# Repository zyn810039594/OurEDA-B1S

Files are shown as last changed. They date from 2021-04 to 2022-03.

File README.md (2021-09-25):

# OurEDA-B1S

一个水下机器人（ROV/AUV）的下位仓控制系统

请使用Arduino、CubeMX、CubeIDE访问相关代码，使用AD打开硬件原理图和PCB Layout设计

### 目录说明

* Board 硬件电路图与PCB layout

  * CtrlBoard

    控制仓（主控仓）电路原理图与PCB layout

  * PowBoard

    电源仓大功率电源电路原理图与PCB layout

  * PowCtrlBoard

    电源仓（PWM控制仓）电路原理图与PCB layout

  * 部分处理姿态控制算法（使用PID）

  * 收集汇总传感器数据（间隔发送本仓传感器（比电源仓多加一个水深传感器）和电源仓传感器数据）

  * 将传感器数据传输到水面端或自主控制仓

  * 接收上位机指令

  * 将指令传给电源仓的H750进行执行

* Sensor

    * DeepF1

        水深传感器数据解析程序

        使用STM32F103C6T6

        * 专用于处理水深传感器的数据

        * 使用Arduino开发

    * GY-39

        温湿度传感器资料

    * P30

        声呐水深传感器资料

        * 使用submodule引用了一个上位机程序

    * WT931

        九轴传感器资料

* CtrlH7

  控制仓STM32H750程序

  * 部分处理姿态控制算法（使用PID）
  * 收集汇总传感器数据（间隔发送本仓传感器（比电源仓多加一个水深传感器）和电源仓传感器数据）
  * 将传感器数据传输到水面端或自主控制仓
  * 接收上位机指令
  * 将指令传给电源仓的H750进行执行

* PowH7

  电源仓控制板STM32H750程序

  * 进行温湿度气压、九轴传感器数据解析
  * 将传感器数据传输到控制仓的STM32H750
  * 接收上位机发送的PWM指令控制所有PWM输出

* MT7621

  机器人视频推流、串口网口转换、网络通讯中心设备

  使用成品MT7621路由器模块

  固件、软件配置、内核版本等

* Debug

  在调试过程中遇到重大Bug的解决方案

* Doc

  整体设计文档

* General

  上位机程序

* surface

  上位机内部Arduino程序

  * 使用Arduino获取操纵旋钮的信号

* DataFormat

  Debug时用到的一些上传/下传数据

### 文件说明

* UpFormat.xlsx

  上传数据格式

* DownFormat.xlsx

  下传指令格式

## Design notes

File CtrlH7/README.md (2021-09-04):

# 控制板STM32H750主程序

最新程序为`file_rebuild` ，移植了新版本的ROV驱动库

该仓的STM32负责漏水检测、温湿度大气压传感器、水深传感器、九轴的控制功能

同时可以自主实现PID定向定深

PID定向模式：保证ROV航向不变

PID定深模式：保证ROV所处深度不变

使用FreeRTOS进行任务调度，但仅仅使用了其中的任务调度功能，并未使用信号量、消息队列等功能（主要是因为原作者懒得用），下一迭代可能会考虑充分使用这些功能以增强系统稳定性

主要文件：

* main.c：分配任务和基本控制逻辑
* BasicCtrl.c：基本控制函数库文件，一直沿用到现在的推进器控制代码
* Sensor.c：传感器处理函数库文件

## 初步测试结果

1. 上电后stm32h7无任何反应
2. 温湿度传感器输出正常
3. 九轴传感器输出正常
4. 深度解算板（stm32f1）输出正常
5. MT7621工作正常，但WAN口无法连接外网，所有LAN口正常工作
6. USB无法连接
7. openwrt开机缓慢

准备进行初步Debug

### Dubug结果

1. 修复路由器模块WAN口问题、USB问题
2. 重新刷写openwrt固件到19.07版本
3. 成功安装需要的软件
4. 修复stm32h750所有问题

## 再次测试结果

1. stm32h750上传数据、下传指令功能正常
2. 未验证上传数据内容是否正常，但是指令长度、传感器变化、开始标志位、结束标志位均存在，待后续测试
3. 未验证下传指令速率，存在未上电时控制指令紊乱的情况
4. 通常USB设备可以连接，但无法连接uvc免驱USB摄像头
5. openwrt可以接收到串口数据，但未测试串口转网口功能
6. openwrt其他功能正常

### 上传数据测试结果

1. 湿度上传**可能**存在问题（正常值60，传感器上报80）
2. 水深上传存在问题
3. 欧拉角上传可能存在问题

### Bug修复结果

1. 修复温湿度大气压传感器数据问题
2. 可能修复欧拉角上传数据问题
3. **发现水深水温传感器数据传输卡死**

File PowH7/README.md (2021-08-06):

# PWM-传感器控制板程序

位于推进器控制仓的STM32主要负责控制PWM输出和接收一部分传感器数据

最新程序为`file_rebuild`，修复了很多问题，并合理使用了FreeRTOS的互斥量、信号量，避免使用全局变量

## 初步测试结果

1. PWM输出正常
2. 传送带PWM输出正常
3. 由于PCB设计问题，继电器无法控制
4. 机械臂PWM缺少两路输出（其他四路工作正常），怀疑缺少上位机指令导致
5. 缺少灯光PWM输出，初步怀疑缺少上位机指令导致
6. 缺少云台PWM输出，初步怀疑缺少上位机指令导致
7. 缺少上传串口信息（两次检测中一次可以读取到十六进制数据，一次无法读取），经检测传感器并未损坏，怀疑是程序问题

## 最终测试结果

1. 修复了继电器问题
2. 数字隔离器损坏导致灯光、云台缺少输出，已修复
3. 机械臂PWM缺少两路输出，修复其中一路（为软件问题），另一路暂时未能修复，原因不明
4. 缺少上传串口信息，怀疑是程序问题
5. 暂未发现其他问题

### Debug结果

1. 通过外挂自制的光耦-继电器模块彻底修复继电器问题
2. 修复所有PWM
3. 发现串口程序问题，无法正常从传感器读取数据上传，准备修复

## 实机测试结果

1. 修复了串口程序问题
2. 基本控制功能正常
3. 无法控制灯光PWM
4. 未验证串口信息发送准确性

### Dubug结果

1. 灯光只能使用4.2V以上电压驱动（典型值5V）
2. 发生串口控制失灵时不灵的情况，怀疑是调整为50Hz的PWM信号问题，已经改回

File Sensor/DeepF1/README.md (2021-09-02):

# 深度数据解析

使用Arduino对STM32F103进行开发

### 依赖库

1. Arduino IDE
2. [Arduino_STM32扩展](https://github.com/rogerclarkmelbourne/Arduino_STM32)
3. MS5883 Arduino库

## 初步测试结果

能够按照既定格式向STM32H750发送解析后的深度数据

## 测试结果

***测试通过***

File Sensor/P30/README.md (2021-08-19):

# 声呐

连接到控制板的stm32上

使用串口UART5

这里引用了一个官方的上位机源码ping-viewer

使用

```shell
git submodule init
git submodule pull
```

拉取submodule

[参考资料](https://searobotix.com/p30-sonar/)

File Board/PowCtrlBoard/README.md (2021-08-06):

# PWM-传感器控制板硬件设计

使用一个STM32H750接收上位机发送的控制数据并控制推进器、云台等PWM输出

同时该MCU会收取传感器上传的数据，解析后再传输给控制板的STM32或AUV控制单元或上位机

## 初步测试结果

继电器控制电路出错

### Debug结果

已对继电器控制电路进行修改，加入洞洞板焊接的光耦-继电器控制电路，参照如下电路设计，但将继电器放在接地一端，采用共地驱动

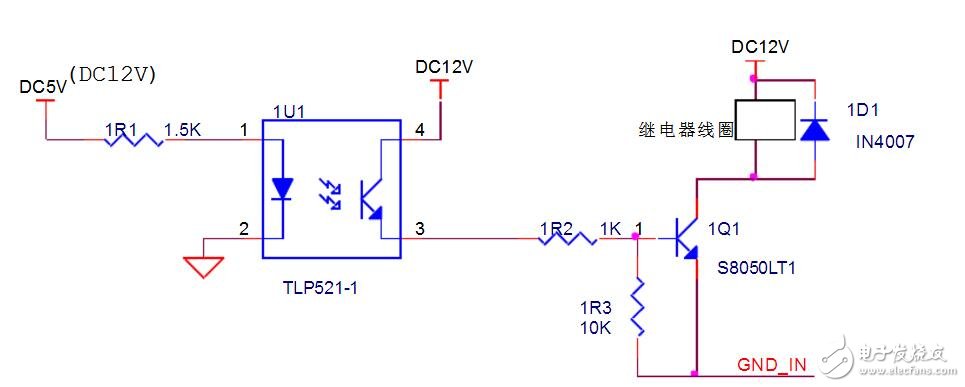
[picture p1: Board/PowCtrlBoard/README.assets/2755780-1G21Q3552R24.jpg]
光耦驱动继电器电路图大全（光电耦合器/ULN2803 /开关电路）


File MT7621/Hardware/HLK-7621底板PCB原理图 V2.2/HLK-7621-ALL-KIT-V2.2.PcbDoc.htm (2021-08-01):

Reporting Options

# File in Previous Format

Date | : | 2021/6/21
Time | : | 10:18:27
Filename | : | E:\HLK\模块资料\资料\wifi模块\HLK-7621A\HLK-7621底板PCB原理图 V2.2\HLK-7621-ALL-KIT-V2.2.PcbDoc

Version | Warning
Summer 09 | CAUTION - File contains old violation objects. These violations are no longer supported & will not be loaded. Please run DRC after opening this file in order to refresh the violations.
Summer 09 | CAUTION - Existing testpoint rules and settings are used as fabrication testpoint information.
Release 12 | CAUTION - Air Gap Width previously controlled by Clearance rule is now controlled by Polygon Connect Style rule's newly introduced Air Gap Width (set to default value). Suggest reviewing each Polygon Connect Style rule's Air Gap Width attribute for correctness.
Release 13 | CAUTION - Silkscreen Over Component Pads Rules are converted to Silk To Solder Mask Clearance Rules. Suggest examining rule scopes for accuracy.

This file was generated by an earlier version of the software

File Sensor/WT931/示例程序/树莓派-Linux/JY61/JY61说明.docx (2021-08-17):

1.给树莓派 连接电源和网线

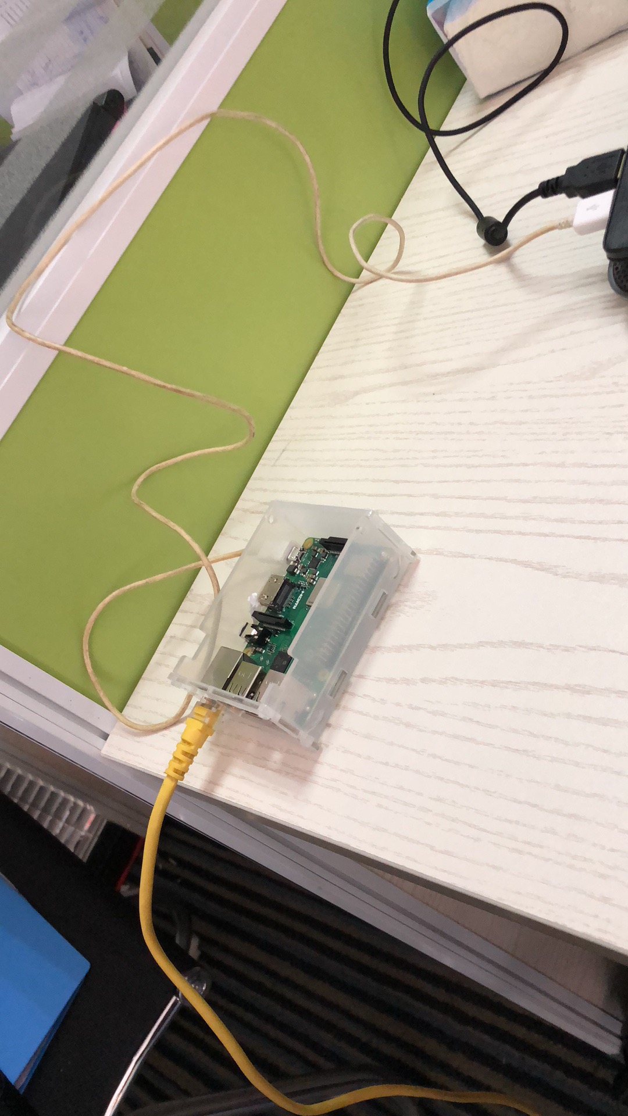
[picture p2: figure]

2.连接上树莓派和JY61的模块（注意六合一串口模块拨码1为ON、拨码2为OFF，开关S1置other ；JY61模块跟六合一串口模块引脚需要一一对应，VCC对3V3,RX对TX，TX对RX，GND对GND）

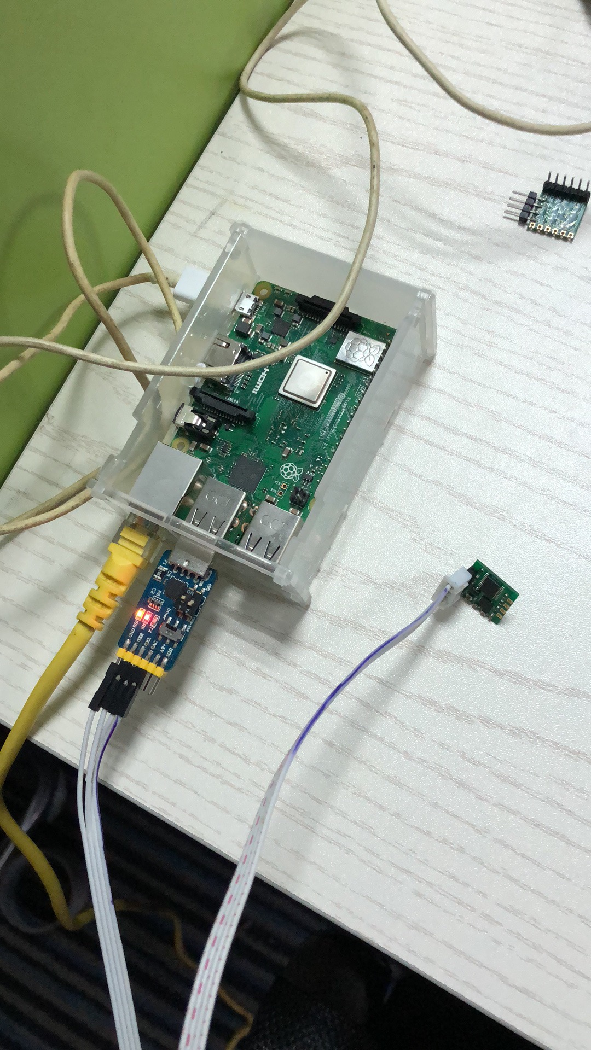
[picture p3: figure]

3.前往官网下载VNC，官网地址：https://www.realvnc.com/en/

软件安装步骤参考官网安装步骤，在下载的文件夹VNC Viewer中打开vncviewer.exe

在这里输入树莓派的ip地址（可通过ip搜索器搜索，选择ip名为raspberrypi的ip地址）

（## IP搜索器可自行百度下载）

4.输入账号密码， 账号：**** 密码：****

账号密码参考自己的树莓派资料

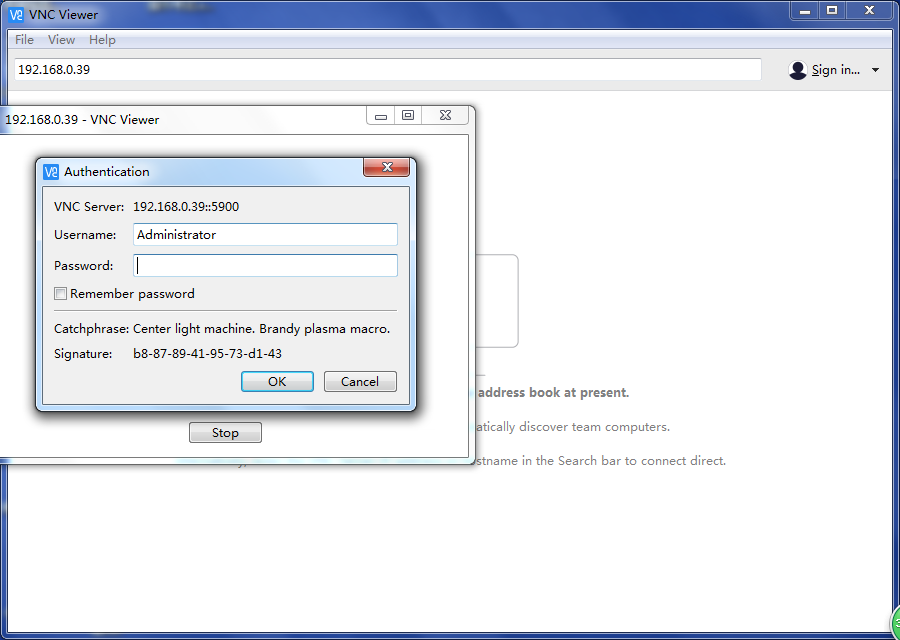
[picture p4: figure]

5.在上中方上传电脑的示例代码文件到树莓派中

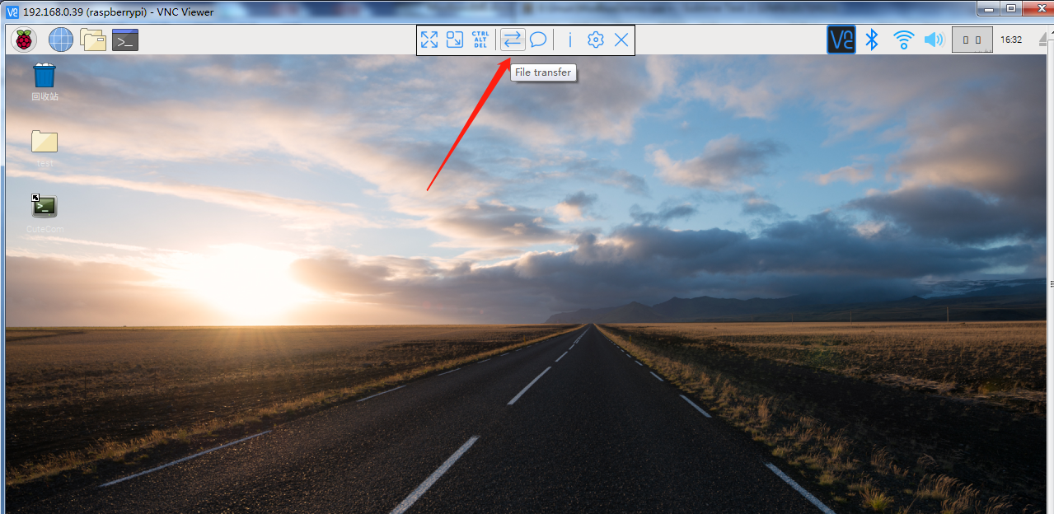
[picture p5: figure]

6.拷贝完成后，打开终端对桌面进行

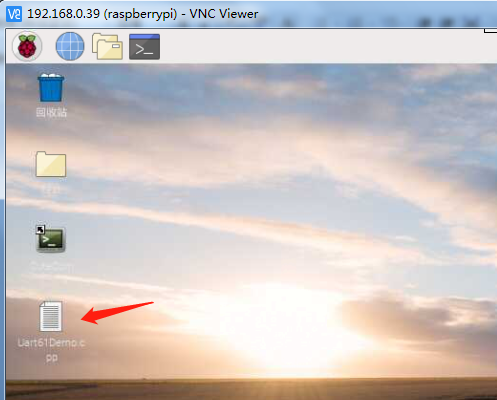
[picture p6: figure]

7.注：右键可打开终端

终端中的Desktop文件夹即为桌面

编辑：gcc Uart61Demo.cpp -o Uart61Demo

运行：./ Uart61Demo

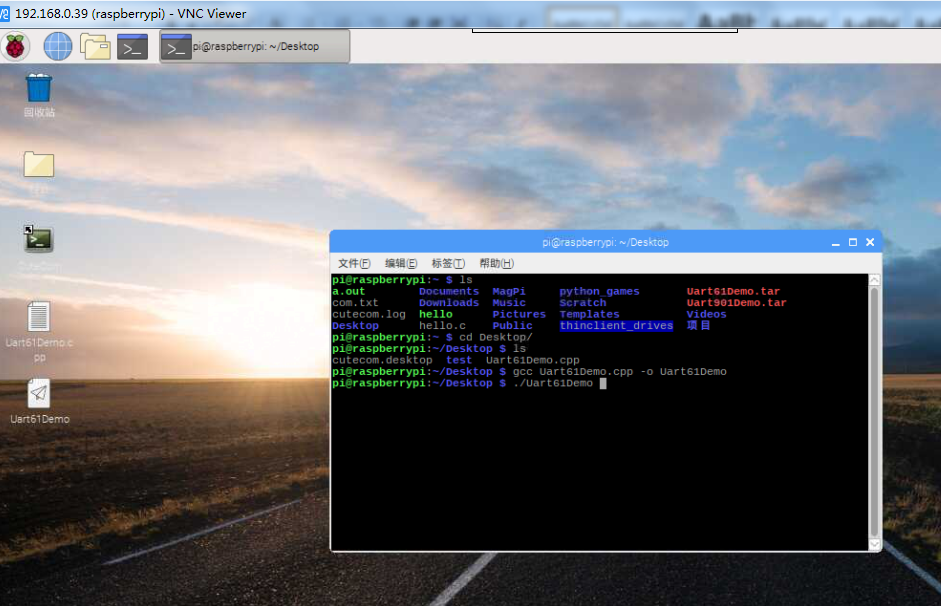
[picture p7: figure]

8.结果展示

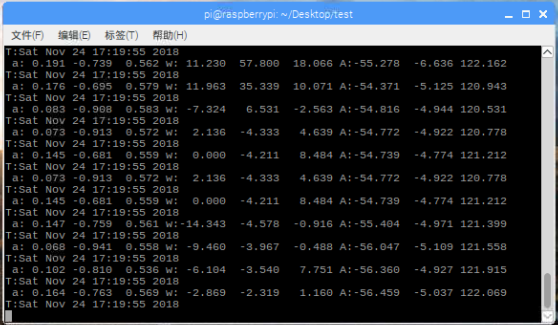
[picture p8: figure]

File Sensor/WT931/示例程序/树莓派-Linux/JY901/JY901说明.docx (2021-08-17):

1.给树莓派 连接电源和网线


2.连接上树莓派和JY901的模块（注意六合一串口模块拨码1为ON、拨码2为OFF，开关S1置other ；JY901模块跟六合一串口模块引脚需要一一对应，VCC对3V3,RX对TX，TX对RX，GND对GND）

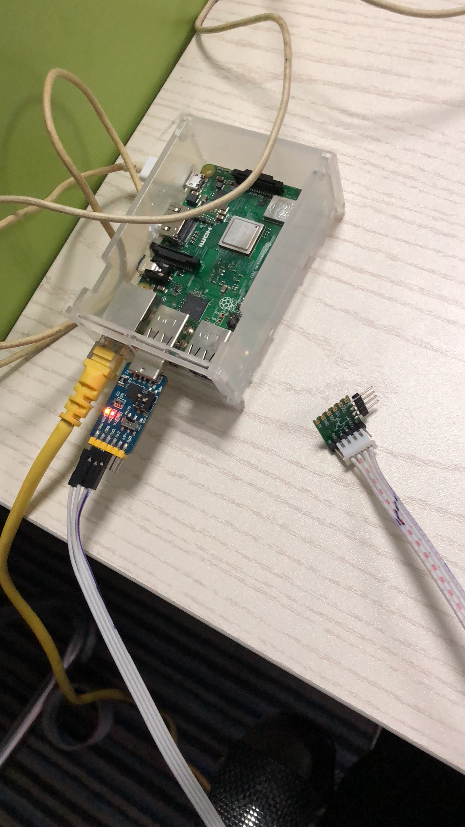
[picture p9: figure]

3.前往官网下载VNC，官网地址：https://www.realvnc.com/en/

软件安装步骤参考官网安装步骤，在下载的文件夹VNC Viewer中打开vncviewer.exe

在这里输入树莓派的ip地址（可通过ip搜索器搜索，选择ip名为raspberrypi的ip地址）

（## IP搜索器可自行百度下载）

4.输入账号密码， 账号：**** 密码：****

账号密码参考自己的树莓派资料


5.在上中方上传电脑的示例代码文件到树莓派中


6.拷贝完成后，打开终端对桌面进行

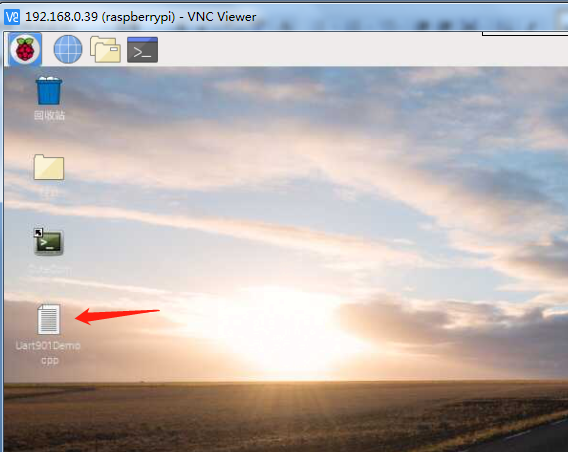
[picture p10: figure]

7.注：右键可打开终端

终端中的Desktop文件夹即为桌面

编辑：gcc Uart901Demo.cpp -o Uart901Demo

运行：./ Uart901Demo

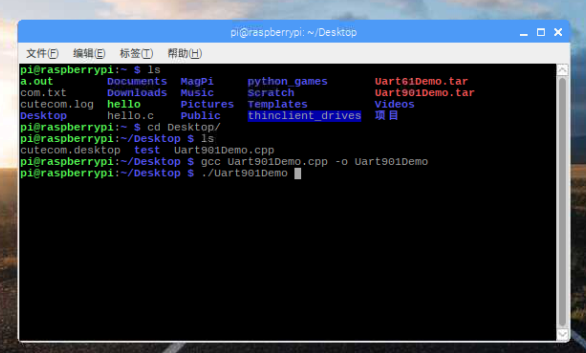
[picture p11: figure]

8.结果展示

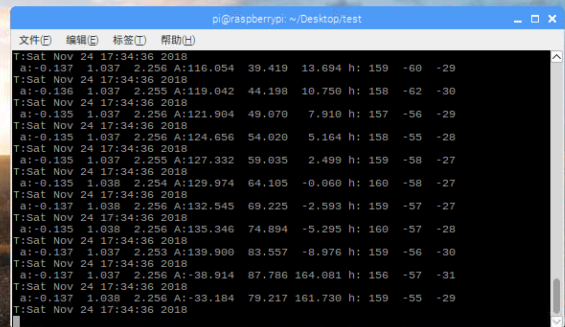
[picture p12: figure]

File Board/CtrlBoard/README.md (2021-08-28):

# 控制板与电源板硬件设计

**horziontal**：第一版叠层5V/3.3V电源板，已废弃

Fatal：存在功率电感容易过流损坏的问题

**horziontal_v2**：第二版叠层5V/3.3V电源板，采用大功率绕线电感并优化了布线

Debug：修正了电感画错（没有旋转90度导致大短路）的问题

**vertical**：直插5V/3.3V电源板，测试阶段未见Bug

Fatal：老师觉得难看

**Processor**：包含PRO和PRO2两版主控板设计，PRO单纯作为留档，PRO2修正了PRO中存在的一些问题。

Debug：IIC接口添加4.7K上拉电阻

Debug：添加JTAG接口

Debug：添加可选的AMS1117辅助供电

**ProConnect**：网口、摄像头转接板

Debug：JP3所接WAN口无法使用（有供电但无信号传输），暂时无法确认是否为PCB问题

Debug：WAN口Bob-Smith电路没有焊好导致无信号，已经修复

### 几个板子都是新手/随意走线，高血压警告

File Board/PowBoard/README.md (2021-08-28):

# 总电源板硬件设计

使用多个堆叠的大功率稳压输出模块输出12V-60A（max），以供给推进器、舵机，并通过`【CtrlBoard】-【horziontal】和【vertical】`两个稳压隔离电源模块输出5V和3.3V为MCU和传感器供电

电路走线使用8oz特殊规格加镀锡铜排加强功率性能

尚未进行测试⚠

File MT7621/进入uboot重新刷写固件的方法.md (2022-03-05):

1. 连接LAN口到上位机
2. 修改LAN口的上位机ip为静态`10.10.10.3`，子网掩码为`255.255.0.0`
3. 将openwrt断电
4. 按住sw_wps按键
5. openwrt上电
6. 保持按键1min
7. 松开按键
8. 打开`10.10.10.123`
9. 选择固件并进行上传
10. 等待2min以上
11. 修改LAN口ip为dhcp模式
12. 尝试连接`192.168.1.1`或`192.168.16.254`或`192.168.1.254`

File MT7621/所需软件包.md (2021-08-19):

1. 推流
   * usb摄像头驱动

     * kmod-usb2
     * kmod-usb-uhci
     * kmod-usb-ohci
     * libv4l
     * kmod-video-core
     * kmod-video-videobuf2
     * kmod-video-uvc
     * kmod-video-pwc
     * kmod-video-gspca-core
     * kmod-video-cpia2
     * kmod-video-gspca-*（有关的包全部安装）

   * mjpg-streamer推流与luci控制

     * mjpg-streamer
     * luci-app-mjpg-streamer
     * luci-i18n-mjpg-streamer-zh-cn

2. 串口-tcp报文转换
   
   * ser2net
   
3. debug工具
   
   * usbutils
   * vim/vi
   * minicom

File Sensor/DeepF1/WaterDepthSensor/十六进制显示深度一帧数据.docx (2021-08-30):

54 3D 32 32 2E 32 35 44 3D 2D 30 2E 30 30 0D 0A

54 3D 32 32 2E 32 39 44 3D 30 2E 30 30 0D 0A

54 3D 32 32 2E 33 32 44 3D 30 2E 30 30 0D 0A

0 1 2 3 4 5 6 7 8 9 10 11 12 13 14

54 3D 32 30 2E 35 33 44 3D 2D 30 2E 30 31 0D 0A3D2E

T = int16 . int16 D = int16 . int16 \r \n

int16[10];

u8 data[16];

大致分析如下

54→‘T’

3D→‘=’

2E→‘.’

44→‘D’

3D→‘=’

2D→‘-’

OD→‘\r’

OA→’\n’

收到的都是字符串，需要转换成十六进制

T | = | int16 | | . | int16 | | D | = | | | . | int16 | | \r | \n
54 | 3d | | | 2e | | | 44 | 3d | | | 2e | | | 0d | 0a
0 | 1 | 2 | 3 | 4 | 5 | 6 | 7 | 8 | 9 | 10 | 11 | 12 | 13 | 14 | 15

T | = | int16 | | . | int16 | | D | = | - | . | int16
54 | 3d | 32 | 32 | 2e | 35 | 35 | 44 | 3d | 2d | 2e | 30 | 30 | 35 | d
0 | 1 | 2 | 3 | 4 | 5 | 6 | 7 | 8 | 9 | 10 | 11 | 12 | 13 | 14

54 3d 32 32 2e 35 35 44 3d 2d 2e 30 30 35 d

0 1 2 3 4 5 6 7 8 9 10 11 12 13 15

T=22.70D=0.03

T=22.70D=0.04

T=22.71D=0.03

T=22.70D=0.03

T=22.70D=0.03

T=22.71D=0.03

T=22.70D=0.03

T=22.71D=0.03

T=22.71D=0.04

T=22.71D=0.03

T=22.71D=0.03

T=22.71D=0.03

T=22.71D=0.03

T=22.71D=0.03

T=22.71D=0.03

T=22.71D=0.04

T=22.71D=0.03

T=22.71D=0.03

T=22.71D=0.04

T=22.71D=0.03

T=22.71D=0.03

54 3D 32 32 2E 37 30 44 3D 30 2E 30 33 0D 0A

54 3D 32 32 2E 36 39 44 3D 30 2E 30 33 0D 0A

54 3D 32 32 2E 37 30 44 3D 30 2E 30 33 0D 0A

54 3D 32 32 2E 37 30 44 3D 30 2E 30 33 0D 0A

54 3D 32 32 2E 37 30 44 3D 30 2E 30 33 0D 0A

54 3D 32 32 2E 37 30 44 3D 30 2E 30 33 0D 0A

54 3D 32 32 2E 36 39 44 3D 30 2E 30 34 0D 0A

54 3D 32 32 2E 37 30 44 3D 30 2E 30 34 0D 0A

54 3D 32 32 2E 37 30 44 3D 30 2E 30 34 0D 0A

54 3D 32 32 2E 37 30 44 3D 30 2E 30 34 0D 0A

54 3D 32 32 2E 37 30 44 3D 30 2E 30 33 0D 0A

54 3D 32 32 2E 37 30 44 3D 30 2E 30 33 0D 0A

54 3D 32 32 2E 37 30 44 3D 30 2E 30 33 0D 0A

54 3D 32 32 2E 37 30 44 3D 30 2E 30 34 0D 0A

54 3D 32 32 2E 37 30 44 3D 30 2E 30 34 0D 0A

54 3D 32 32 2E 37 30 44 3D 30 2E 30 34 0D 0A

54 3D 32 32 2E 37 30 44 3D 30 2E 30 33 0D 0A

54 3D 32 32 2E 37 30 44 3D 30 2E 30 33 0D 0A

54 3D 32 32 2E 37 30 44 3D 30 2E 30 33 0D 0A

54 3D 32 32 2E 37 30 44 3D 30 2E 30 33 0D 0A

54 3D 32 32 2E 37 30 44 3D 30 2E 30 33 0D 0A

54 3D 32 32 2E 37 30 44 3D 30 2E 30 34 0D 0A

54 3D 32 32 2E 37 30 44 3D 30 2E 30 33 0D 0A

54 3D 32 32 2E 37 30 44 3D 30 2E 30 34 0D 0A

54 3D 32 32 2E 37 31 44 3D 30 2E 30 33 0D 0A

54 3D 32 32 2E 37 30 44 3D 30 2E 30 33 0D 0A

54 3D 32 32 2E 37 30 44 3D 30 2E 30 33 0D 0A

54 3D 32 32 2E 37 31 44 3D 30 2E 30 33 0D 0A

54 3D 32 32 2E 37 30 44 3D 30 2E 30 33 0D 0A

54 3D 32 32 2E 37 31 44 3D 30 2E 30 33 0D 0A

54 3D 32 32 2E 37 31 44 3D 30 2E 30 34 0D 0A

54 3D 32 32 2E 37 31 44 3D 30 2E 30 33 0D 0A

54 3D 32 32 2E 37 31 44 3D 30 2E 30 33 0D 0A

54 3D 32 32 2E 37 31 44 3D 30 2E 30 33 0D 0A

54 3D 32 32 2E 37 31 44 3D 30 2E 30 33 0D 0A

54 3D 32 32 2E 37 31 44 3D 30 2E 30 33 0D 0A

54 3D 32 32 2E 37 31 44 3D 30 2E 30 33 0D 0A

54 3D 32 32 2E 37 31 44 3D 30 2E 30 34 0D 0A

54 3D 32 32 2E 37 31 44 3D 30 2E 30 33 0D 0A

54 3D 32 32 2E 37 31 44 3D 30 2E 30 33 0D 0A

54 3D 32 32 2E 37 31 44 3D 30 2E 30 34 0D 0A

54 3D 32 32 2E 37 31 44 3D 30 2E 30 33 0D 0A

54 3D 32 32 2E 37 31 44 3D 30 2E 30 33 0D 0A

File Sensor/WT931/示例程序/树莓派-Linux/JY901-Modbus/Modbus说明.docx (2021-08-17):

1.给树莓派 连接电源和网线


2.连接上树莓派和485系列的模块（注意六合一串口模块拨码1、拨码2都为ON，开关S1置other ；485系列模块跟六合一串口模块引脚需要一一对应，VCC对3V3,A对A，B对B，GND对GND）

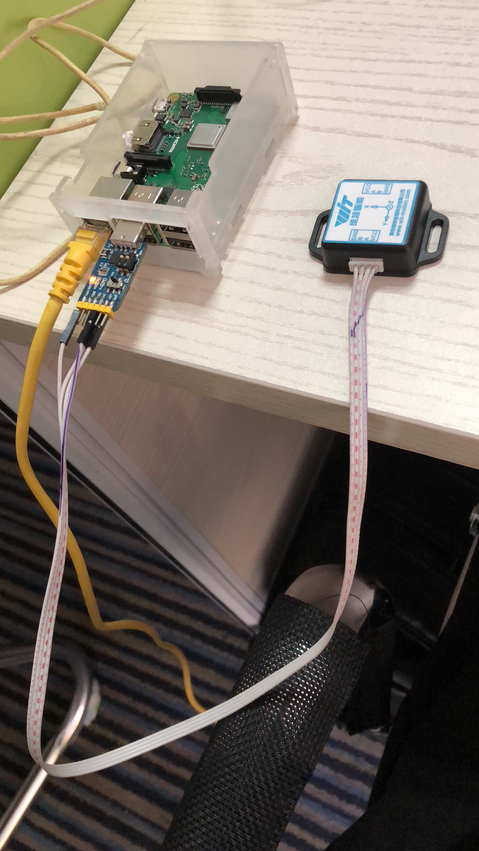
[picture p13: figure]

3.前往官网下载VNC，官网地址：https://www.realvnc.com/en/

软件安装步骤参考官网安装步骤，在下载的文件夹VNC Viewer中打开vncviewer.exe

在这里输入树莓派的ip地址（可通过ip搜索器搜索，选择ip名为raspberrypi的ip地址）

（## IP搜索器可自行百度下载）

4.输入账号密码， 账号：**** 密码：****

账号密码参考自己的树莓派资料


5.在上中方上传电脑的示例代码文件到树莓派中


6.拷贝完成后，打开终端对桌面进行

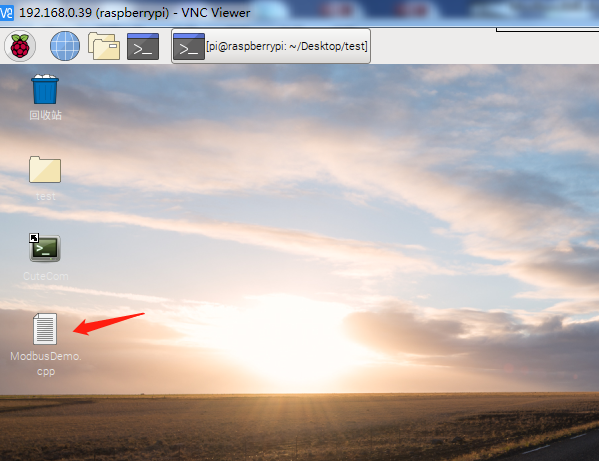
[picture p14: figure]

7.注：右键可打开终端

终端中的Desktop文件夹即为桌面

编辑：gcc ModbusDemo.cpp -o ModbusDemo

运行：./ModbusDemo

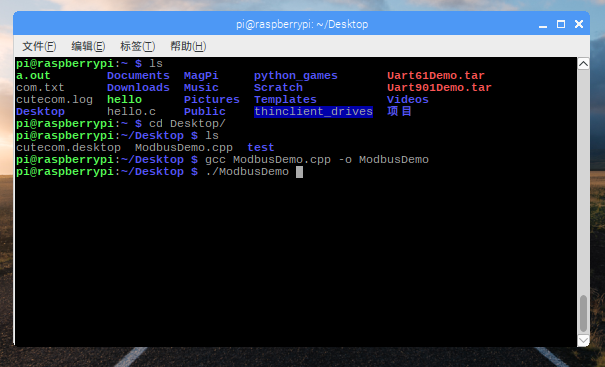
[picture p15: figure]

8.结果展示

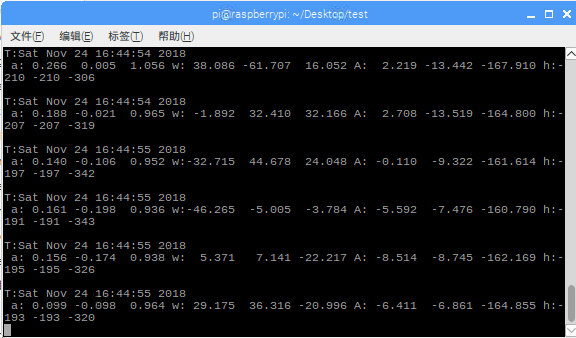
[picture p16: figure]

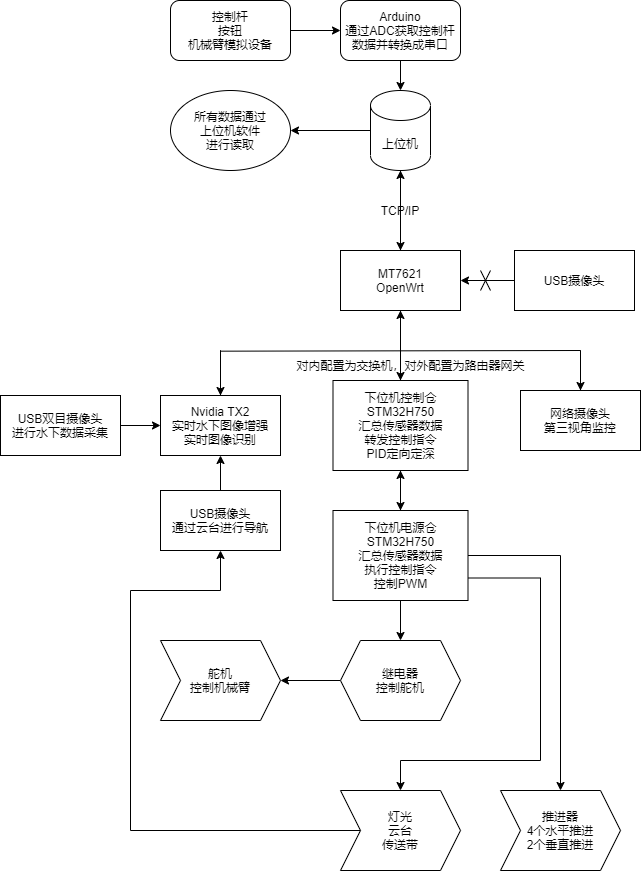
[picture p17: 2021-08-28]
Doc/General.png

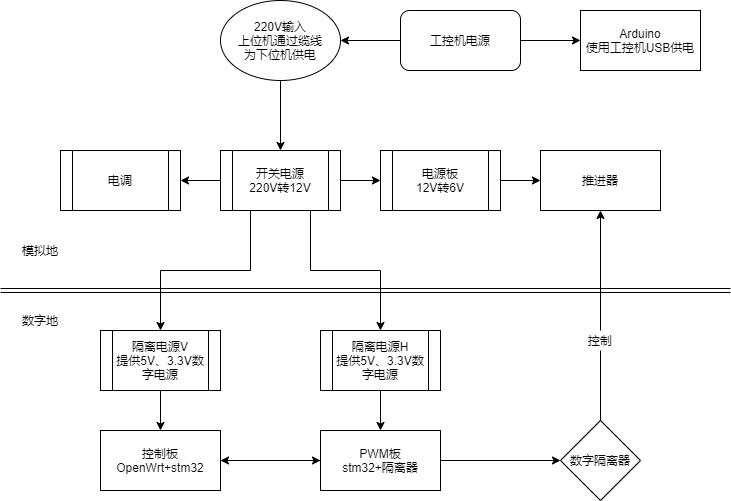
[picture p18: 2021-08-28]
Doc/Power.png

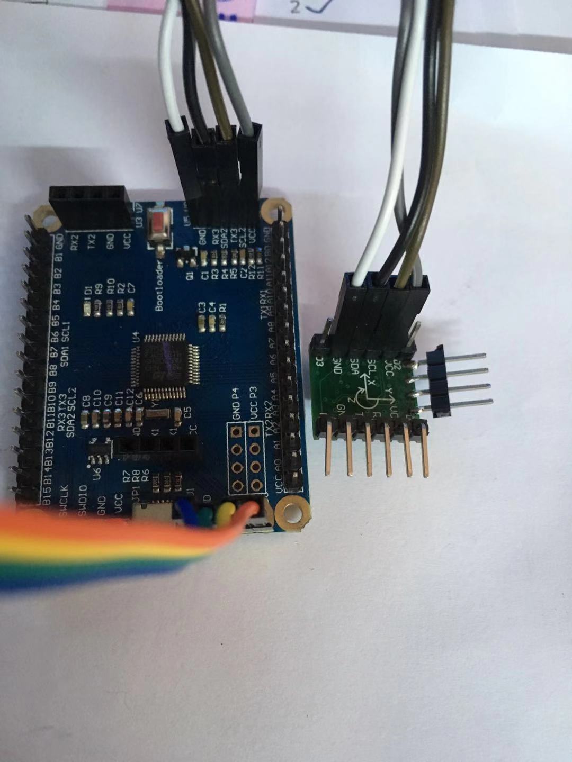
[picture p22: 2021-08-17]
Sensor/WT931/示例程序/STM32/STM32Core IIC写入校准指令/IIC连接图.jpg

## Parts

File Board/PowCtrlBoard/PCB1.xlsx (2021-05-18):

Comment | Description | Footprint | LibRef | Quantity
10uF | 钽电容 | CASE-B_3528 | 3528 100uF (107) 10% 6.3V | 10
0.1uF | 贴片电容 | 0603_C | 0603 100nF (104) 10% 50V | 10
1uF (105) 10% 50V | 贴片电容 | 1206_C | 1206 1uF (105) 10% 50V | 1
1.25T-2AW_C722634 | GH1.25立贴座 | GH-1.25 | GH 1.25T-2AW_C722634 | 4
1N4148WS T4 | 二极管 | SOD-323 | SOD-323 1N4148WS T4 | 1
PH2.0-3P | 3P PH2.0立针座 | PH2.0-3P | PH2.0-3P | 3
PH2.0-2P | 2P PH2.0立针座 | PH2.0-2P | PH2.0-2P | 3
Female HDR1X4 | 四脚排母 | Fe-HDR1X4/2.54-S | Female HDR1X4 | 4
Female HDR1X7 | 七脚排母 | Fe-HDR1X7/2.54-S | Female HDR1X7 | 4
排针-座 2*4 | 2*4排针 | 排针-座 2*4 | 排针-座 2*4 | 1
HDR-1X2 | 2P接插件 | KF128-5.08-2P | Header 2 | 2
SS8550 Y2 | 三极管 | SOT-23(SOT-23-3) | SOT-23 SS8550 Y2 | 1
SI2302 | MOS(场效应管) | SOT-23(SOT-23-3) | 2N7002 7002 | 1
5.1KΩ (5101) ±1% | 贴片电阻 | 0805_R | 0805 5.1KΩ (5101) 1% | 5
330Ω (3300) ±1% | 贴片电阻 | 0805_R | 0805 330Ω (3300) 1% | 1
10KΩ (1002) ±1% | 贴片电阻 | 0603_R | 0603 10KΩ (1002) 1% | 1
4.7KΩ (4701) ±1% | 贴片电阻 | 0603_R | 0603 4.7KΩ (4701) 1% | 1
27KΩ (2702) ±1% | 贴片电阻 | 0603_R | 0603 27KΩ (2702) 1% | 1
1KΩ (1001) ±1% | 贴片电阻 | 0603_R | 0603 1KΩ (1001) 1% | 2
ISOW7840 | 数字隔离器7840 | ISOW7840 | ISOW7840 | 5
0.01uF | 无极性贴片电容 | C 0603_M | C | 1
0.1uF | 无极性贴片电容 | C 0805_L | C | 1
0.1u | 无极性贴片电容 | C 0603_M | C | 20
0.01u | 无极性贴片电容 | C 0603_M | C | 2
DIP-8插座 | DIP-8插座 | DIP-8座 | DIP-8插座 | 1
Header 8X2 | 8*2P IDC接插件 | IDC2.54-LI-2x8P | Header 8X2 | 4
HDR-1X4 | 4P MX1.25立贴 | MX 1.25-LS-4P | Header 4 | 1
PHB2.0 | 4*2P PHB2.0立插 | PHB2.0-LI-2x4P | Header 4X2 | 5
HDR-1X3 | PH2.0 3P立贴 | PH2.0-WI-3P | Header 3 | 1
HDR-1X2 | KF128 2P接插件 | KF128-5.08-2P | Header 2 | 7
HDR-1X8 | KF128 8P接插件 | KF128-5.08-8P | Header 8 | 1
水深解算 | 20脚排母 | Fe-HDR1X20/2.54-S | Female HDR1X20 | 2
SS8550 | 高频放大-PNP型 | SOT23-3M | 8550-SMD | 1
10K | 贴片电阻 | R 0603_M | R | 2
330 | 贴片电阻 | R 0805_L | R | 1
75 | 贴片电阻 | R 0603_M | R | 20
27K | 贴片电阻 | R 0603_M | R | 1
1K | 贴片电阻 | R 0603_M | R | 2
240 | 贴片电阻 | R 0603_M | R | 1
SG24002G | 网络变压器 | SG24002G | SG24002G | 5
1uF/50V | 直插瓷片电容 | CC 2.2*5 | C-CC | 9
100uF/高频低阻 | 高频低阻电解电容 | CAP 3.5*8*11.5-H - GD | C-CAP | 6
1nF/250V | 安规Y电容 | CY 7.5*10*4 | C-CY | 3
470uF/50V | 贴片电解电容 | CM G(12.5*13.5) | C-CM | 6
10uF/6.3V | 贴片钽电容 | CD A(3216) | C-CD | 4
SRF0905-202Y | 贴片共模电感 | SRF0905 | SRF0905-202Y | 3
4.7uH | 贴片线圈电感 | NR5020 | DML-5020 | 3
2.2uH | 功率贴片电感 | L 0805 | L | 3
10uH | 功率贴片电感 | L 0805 | L | 3
14D330k | 压敏电阻 | 14D330k | 14D330k | 3
10D1205B | DC-DC降压模块 | 10D1205B | 10D1205B | 3
AIC1084-33CM | 大功率LDO | TO263-3B | AIC1084-33CM | 2
10u | 无极性贴片电容 | C 0603_M | C | 2
0.1u | 无极性贴片电容 | C 0603_M | C | 2
HDR-1X4 | 4P PH2.0立贴 | PH2.0-LS-4P | Header 4 | 4
ISOW7841 | 数字隔离器7841 | 7840 | ISOW7841 | 1

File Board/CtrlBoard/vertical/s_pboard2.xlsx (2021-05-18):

Comment | Description | Designator | Footprint | LibRef | Quantity
1uF/50V | 直插瓷片电容 | C0, C1, C4 | CC 2.2*5 | C-CC | 3
100uF/高频低阻 | 直插电解电容 | C2, C3 | CAP 3.5*8*11.5-H - GD | C-CAP | 2
1nF/250V | 高压陶瓷电容，Y电容 | CY1 | CY 7.5*10*4 | C-CY | 1
470uF/50V | 贴片电解电容 | E1, E2 | CM G(12.5*13.5) | C-CM | 2
10uF/6.3V | 贴片钽电容 | E5, E6 | CD A(3216) | C-CD | 2
排针-侧 2*4 |  | JP1, JP2 | 排针-侧 2*4 | 排针-侧 2*4 | 2
SRF0905-202Y | 共模电感 | L1 | SRF0905 | SRF0905-202Y | 1
4.7uH | 差模电感 | L2 | NR5020 | DML-5020 | 1
2.2uH | 小功率贴片电感 | L3 | L 0805 | L | 1
10uH | 小功率贴片电感 | L4 | L 0805 | L | 1
14D330k |  | R1 | 14D330k | 14D330k | 1
10D1205B |  | U1 | 10D1205B | 10D1205B | 1
AIC1084-33CM |  | U3 | TO263-3B | AIC1084-33CM | 1

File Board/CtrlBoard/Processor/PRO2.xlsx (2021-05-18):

Comment | Description | Designator | Footprint | LibRef | Quantity
0.01uF | 无极性贴片电容 | C0 | C 0603_M | C | 1
0.1uF | 无极性贴片电容 | C1 | C 0805_L | C | 1
0.1u | 无极性贴片电容 | C6, C7, C8, C9, C10, C11, C12, C13, C14, C15, C16, C17, C18, C19, C20, C21, C22, C23, C30, C31 | C 0603_M | C | 20
0.01u | 无极性贴片电容 | C24, C25 | C 0603_M | C | 2
DIP-8插座 |  | JP1 | DIP-8座 | DIP-8插座 | 1
Header 8X2 | 8*2P接插件 | JP2, JP3 | IDC2.54-LI-2x8P | Header 8X2 | 2
HDR-1X4 | 4P接插件 | JP5 | MX 1.25-LS-4P | Header 4 | 1
水面 | 4*2P接插件 | JP6 | PHB2.0-LI-2x4P | Header 4X2 | 1
TX2 | 4*2P接插件 | JP7 | PHB2.0-LI-2x4P | Header 4X2 | 1
预留 | 4*2P接插件 | JP8 | PHB2.0-LI-2x4P | Header 4X2 | 1
HDR-1X3 | 3P接插件 | JP11 | PH2.0-WI-3P | Header 3 | 1
HDR-1X2 | 2P接插件 | JP12, JP13 | GH1.25 | Header 2 | 2
HDR-1X2 | 2P接插件 | JP17, JP19 | KF128-5.08-2P | Header 2 | 2
HDR-1X8 | 8P接插件 | JP20 | KF128-5.08-8P | Header 8 | 1
FK750M2-VBT6核心板 |  | M1 | FK750M2-VBT6(精简版) | FK750M2-VBT6 | 1
GY-39 | 气压温湿度光强传感器 | M2 | GY-39 | GY-39 | 1
WT-931 | WT-931姿态角度传感器 | M3 | WT-931 | WT-931 | 1
水深解算32 | 水深传感器解算用的stm32模块 | M4 | Deep_32 | Deep_32 | 1
HLK7621 |  | M6 | HLK7621 | HLK7621 | 1
降压模块 |  | M7 | 一号电压板 | 一号电压板 | 1
SS8550 | 高频放大-PNP型 | Q1 | SOT23-3M | 8550-SMD | 1
10K | 贴片电阻 | R1 | R 0603_M | R | 1
330 | 贴片电阻 | R2 | R 0805_L | R | 1
75 | 贴片电阻 | R4, R5, R6, R7, R8, R9, R10, R11, R12, R13, R14, R15, R16, R17, R18, R19, R20, R21, R22, R23 | R 0603_M | R | 20
27K | 贴片电阻 | R24 | R 0603_M | R | 1
1K | 贴片电阻 | R25, R26 | R 0603_M | R | 2
240 | 贴片电阻 | R27 | R 0603_M | R | 1
SG24002G |  | T1, T2, T3, T4, T5 | SG24002G | SG24002G | 5

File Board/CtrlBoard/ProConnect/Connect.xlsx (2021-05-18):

Comment | Description | Designator | Footprint | LibRef | Quantity
10u | 无极性贴片电容 | C1, C3 | C 0603_M | C | 2
0.1u | 无极性贴片电容 | C2, C4 | C 0603_M | C | 2
Header 8X2 | 8*2P接插件 | JP1, JP2 | IDC2.54-LI-2x8P | Header 8X2 | 2
预留 | 4*2P接插件 | JP3, JP4 | PHB2.0-LI-2x4P | Header 4X2 | 2
HDR-1X4 | 4P接插件 | JP5, JP6, JP7, JP8 | PH2.0-LS-4P | Header 4 | 4
HDR-1X2 | 2P接插件 | JP9 | HDR2.54-LI-2P | Header 2 | 1
HDR-1X2 | 2P接插件 | JP9 | KF128-5.08-2P | Header 2 | 1
ISOW7841 |  | M1 | 7840 | ISOW7841 | 1
10K | 贴片电阻 | R1 | R 0603_M | R | 1

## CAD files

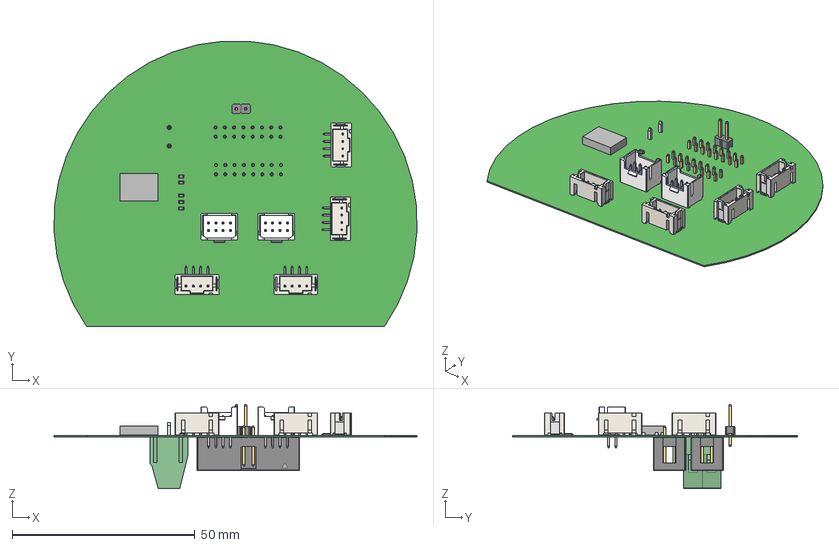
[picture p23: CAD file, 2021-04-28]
Board/CtrlBoard/ProConnect/Connect.step
99.4 x 78.2 x 23.1 mm
Board
R_0603
LOGO? x 9
Extruded
HDR2.54-1P x 2
KF128-5.08 x 2
LOGO?0.75 x 2
PH2.0-LS-竘褐 x 16
LOGO?0.4 x 4
PH2.0-LS-4P x 4
PHB2.0_竘褐 x 16
LOGO?0.25 x 2
PHB2.0_2x4 x 2
IDC2.54-16P x 2
C_0603 x 4

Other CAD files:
Sensor/GY-39/通信例程/C51/c51_iic/output/main.obj
Sensor/GY-39/通信例程/C51/c51_usart/output/main.obj
Sensor/GY-39/通信例程/C51/c51_iic/output/iic.obj
Sensor/GY-39/通信例程/C51/c51_usart/output/stc_it.obj
Sensor/WT931/示例程序/51/STARTUP.OBJ
Sensor/WT931/示例程序/51/JY901.OBJ
Sensor/GY-39/通信例程/C51/c51_iic/output/stc_it.obj
Sensor/GY-39/通信例程/C51/c51_usart/output/usart.obj
Sensor/WT931/示例程序/51/test.OBJ
Sensor/GY-39/通信例程/C51/c51_iic/output/usart.obj

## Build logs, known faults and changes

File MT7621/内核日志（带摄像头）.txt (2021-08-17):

[    0.000000] Linux version 4.14.221 (haroldzhao@ubuntu) (gcc version 7.5.0 (OpenWrt GCC 7.5.0 r11306-c4a6851c72)) #0 SMP Mon Feb 15 15:22:37 2021
[    0.000000] SoC Type: MediaTek MT7621 ver:1 eco:3
[    0.000000] bootconsole [early0] enabled
[    0.000000] CPU0 revision is: 0001992f (MIPS 1004Kc)
[    0.000000] MIPS: machine is Mediatek AP-MT7621A-V60 EVB
[    0.000000] Determined physical RAM map:
[    0.000000]  memory: 08000000 @ 00000000 (usable)
[    0.000000] Initrd not found or empty - disabling initrd
[    0.000000] VPE topology {2} total 2
[    0.000000] Primary instruction cache 32kB, VIPT, 4-way, linesize 32 bytes.
[    0.000000] Primary data cache 32kB, 4-way, PIPT, no aliases, linesize 32 bytes
[    0.000000] MIPS secondary cache 256kB, 8-way, linesize 32 bytes.
[    0.000000] Zone ranges:
[    0.000000]   Normal   [mem 0x0000000000000000-0x0000000007ffffff]
[    0.000000]   HighMem  empty
[    0.000000] Movable zone start for each node
[    0.000000] Early memory node ranges
[    0.000000]   node   0: [mem 0x0000000000000000-0x0000000007ffffff]
[    0.000000] Initmem setup node 0 [mem 0x0000000000000000-0x0000000007ffffff]
[    0.000000] On node 0 totalpages: 32768
[    0.000000] free_area_init_node: node 0, pgdat 805a8420, node_mem_map 81003000
[    0.000000]   Normal zone: 256 pages used for memmap
[    0.000000]   Normal zone: 0 pages reserved
[    0.000000]   Normal zone: 32768 pages, LIFO batch:7
[    0.000000] random: get_random_bytes called from start_kernel+0x94/0x4ac with crng_init=0
[    0.000000] percpu: Embedded 14 pages/cpu s26192 r8192 d22960 u57344
[    0.000000] pcpu-alloc: s26192 r8192 d22960 u57344 alloc=14*4096
[    0.000000] pcpu-alloc: [0] 0 [0] 1 
[    0.000000] Built 1 zonelists, mobility grouping on.  Total pages: 32512
[    0.000000] Kernel command line: console=ttyS0,57600 rootfstype=squashfs,jffs2
[    0.000000] PID hash table entries: 512 (order: -1, 2048 bytes)
[    0.000000] Dentry cache hash table entries: 16384 (order: 4, 65536 bytes)
[    0.000000] Inode-cache hash table entries: 8192 (order: 3, 32768 bytes)
[    0.000000] Writing ErrCtl register=00066650
[    0.000000] Readback ErrCtl register=00066650
[    0.000000] Memory: 122436K/131072K available (4548K kernel code, 232K rwdata, 1012K rodata, 1236K init, 248K bss, 8636K reserved, 0K cma-reserved, 0K highmem)
[    0.000000] SLUB: HWalign=32, Order=0-3, MinObjects=0, CPUs=2, Nodes=1
[    0.000000] Hierarchical RCU implementation.
[    0.000000] 	RCU restricting CPUs from NR_CPUS=4 to nr_cpu_ids=2.
[    0.000000] RCU: Adjusting geometry for rcu_fanout_leaf=16, nr_cpu_ids=2
[    0.000000] NR_IRQS: 256
[    0.000000] CPU Clock: 1000MHz
[    0.000000] clocksource: GIC: mask: 0xffffffffffffffff max_cycles: 0x1cd42e4dffb, max_idle_ns: 881590591483 ns
[    0.000000] clocksource: MIPS: mask: 0xffffffff max_cycles: 0xffffffff, max_idle_ns: 3822520893 ns
[    0.000008] sched_clock: 32 bits at 500MHz, resolution 2ns, wraps every 4294967295ns
[    0.015485] Calibrating delay loop... 666.41 BogoMIPS (lpj=3332096)
[    0.087798] pid_max: default: 32768 minimum: 301
[    0.097074] Mount-cache hash table entries: 1024 (order: 0, 4096 bytes)
[    0.110100] Mountpoint-cache hash table entries: 1024 (order: 0, 4096 bytes)
[    0.125487] Hierarchical SRCU implementation.
[    0.134679] smp: Bringing up secondary CPUs ...
[    0.144544] Primary instruction cache 32kB, VIPT, 4-way, linesize 32 bytes.
[    0.144551] Primary data cache 32kB, 4-way, PIPT, no aliases, linesize 32 bytes
[    0.144561] MIPS secondary cache 256kB, 8-way, linesize 32 bytes.
[    0.144689] CPU1 revision is: 0001992f (MIPS 1004Kc)
[    0.204297] Synchronize counters for CPU 1: done.
[    0.263933] smp: Brought up 1 node, 2 CPUs
[    0.275079] clocksource: jiffies: mask: 0xffffffff max_cycles: 0xffffffff, max_idle_ns: 19112604462750000 ns
[    0.294539] futex hash table entries: 512 (order: 2, 16384 bytes)
[    0.306737] pinctrl core: initialized pinctrl subsystem
[    0.318250] NET: Registered protocol family 16
[    0.337132] FPU Affinity set after 13320 emulations
[    0.337746] pull PCIe RST: RALINK_RSTCTRL = 4000000
[    0.647812] release PCIe RST: RALINK_RSTCTRL = 7000000
[    0.657875] ***** Xtal 40MHz *****
[    0.664604] release PCIe RST: RALINK_RSTCTRL = 7000000
[    0.674812] Port 0 N_FTS = 1b102800
[    0.681712] Port 1 N_FTS = 1b102800
[    0.688637] Port 2 N_FTS = 1b102800
[    1.847479] PCIE0 no card, disable it(RST&CLK)
[    1.856163] PCIE1 no card, disable it(RST&CLK)
[    1.864962] PCIE2 no card, disable it(RST&CLK)
[    1.884626] mt7621_gpio 1e000600.gpio: registering 32 gpios
[    1.895859] mt7621_gpio 1e000600.gpio: registering 32 gpios
[    1.907037] mt7621_gpio 1e000600.gpio: registering 32 gpios
[    1.919516] i2c-mt7621 1e000900.i2c: clock 100KHz, re-start not support
[    1.934231] clocksource: Switched to clocksource GIC
[    1.945375] NET: Registered protocol family 2
[    1.954701] TCP established hash table entries: 1024 (order: 0, 4096 bytes)
[    1.968464] TCP bind hash table entries: 1024 (order: 1, 8192 bytes)
[    1.981042] TCP: Hash tables configured (established 1024 bind 1024)
[    1.993762] UDP hash table entries: 256 (order: 1, 8192 bytes)
[    2.005256] UDP-Lite hash table entries: 256 (order: 1, 8192 bytes)
[    2.017868] NET: Registered protocol family 1
[    2.026424] PCI: CLS 0 bytes, default 32
[    2.254244] 4 CPUs re-calibrate udelay(lpj = 3325952)
[    2.265203] Crashlog allocated RAM at address 0x3f00000
[    2.275940] workingset: timestamp_bits=30 max_order=15 bucket_order=0
[    2.295809] squashfs: version 4.0 (2009/01/31) Phillip Lougher
[    2.307328] jffs2: version 2.2 (NAND) (SUMMARY) (LZMA) (RTIME) (CMODE_PRIORITY) (c) 2001-2006 Red Hat, Inc.
[    2.330210] io scheduler noop registered
[    2.337880] io scheduler deadline registered (default)
[    2.349302] Serial: 8250/16550 driver, 3 ports, IRQ sharing disabled
[    2.363250] console [ttyS0] disabled
[    2.370327] 1e000c00.uartlite: ttyS0 at MMIO 0x1e000c00 (irq = 16, base_baud = 3125000) is a 16550A
[    2.388231] console [ttyS0] enabled
[    2.402022] bootconsole [early0] disabled
[    2.419669] MediaTek Nand driver init, version v2.1 Fix AHB virt2phys error
[    2.433948] spi-mt7621 1e000b00.spi: sys_freq: 250000000
[    2.445285] m25p80 spi0.0: found w25q256, expected mx25l6405d
[    2.458156] random: fast init done
[    2.465852] m25p80 spi0.0: w25q256 (32768 Kbytes)
[    2.475257] 4 fixed-partitions partitions found on MTD device spi0.0
[    2.487910] Creating 4 MTD partitions on "spi0.0":
[    2.497455] 0x000000000000-0x000000030000 : "u-boot"
[    2.508393] 0x000000030000-0x000000040000 : "u-boot-env"
[    2.519949] 0x000000040000-0x000000050000 : "factory"
[    2.531003] 0x000000050000-0x000000800000 : "firmware"
[    2.542347] 2 uimage-fw partitions found on MTD device firmware
[    2.554173] Creating 2 MTD partitions on "firmware":
[    2.564078] 0x000000000000-0x0000001d5da1 : "kernel"
[    2.574953] 0x0000001d5da1-0x0000007b0000 : "rootfs"
[    2.585768] mtd: device 5 (rootfs) set to be root filesystem
[    2.597166] 1 squashfs-split partitions found on MTD device rootfs
[    2.609499] 0x0000003b0000-0x0000007b0000 : "rootfs_data"
[    2.621851] libphy: Fixed MDIO Bus: probed
[    2.696227] libphy: mdio: probed
[    4.102234] mtk_soc_eth 1e100000.ethernet: loaded mt7530 driver
[    4.114716] mtk_soc_eth 1e100000.ethernet eth0: mediatek frame engine at 0xbe100000, irq 20
[    4.133985] NET: Registered protocol family 10
[    4.144283] Segment Routing with IPv6
[    4.151659] NET: Registered protocol family 17
[    4.160586] 8021q: 802.1Q VLAN Support v1.8
[    4.171121] hctosys: unable to open rtc device (rtc0)
[    4.188430] VFS: Mounted root (squashfs filesystem) readonly on device 31:5.
[    4.206824] Freeing unused kernel memory: 1236K
[    4.215960] This architecture does not have kernel memory protection.
[    5.058062] init: Console is alive
[    5.065130] init: - watchdog -
[    5.415801] kmodloader: loading kernel modules from /etc/modules-boot.d/*
[    5.478919] usbcore: registered new interface driver usbfs
[    5.490048] usbcore: registered new interface driver hub
[    5.502366] usbcore: registered new device driver usb
[    5.520628] xhci-mtk 1e1c0000.xhci: 1e1c0000.xhci supply vbus not found, using dummy regulator
[    5.537943] xhci-mtk 1e1c0000.xhci: 1e1c0000.xhci supply vusb33 not found, using dummy regulator
[    5.558313] xhci-mtk 1e1c0000.xhci: xHCI Host Controller
[    5.570468] xhci-mtk 1e1c0000.xhci: new USB bus registered, assigned bus number 1
[    5.594385] xhci-mtk 1e1c0000.xhci: hcc params 0x01401198 hci version 0x96 quirks 0x0000000000210010
[    5.612672] xhci-mtk 1e1c0000.xhci: irq 19, io mem 0x1e1c0000
[    5.625477] hub 1-0:1.0: USB hub found
[    5.633167] hub 1-0:1.0: 2 ports detected
[    5.642014] xhci-mtk 1e1c0000.xhci: xHCI Host Controller
[    5.653467] xhci-mtk 1e1c0000.xhci: new USB bus registered, assigned bus number 2
[    5.668719] xhci-mtk 1e1c0000.xhci: Host supports USB 3.0  SuperSpeed
[    5.682725] usb usb2: We don't know the algorithms for LPM for this host, disabling LPM.
[    5.701640] hub 2-0:1.0: USB hub found
[    5.710107] hub 2-0:1.0: 1 port detected
[    5.722958] kmodloader: done loading kernel modules from /etc/modules-boot.d/*
[    5.754544] init: - preinit -
[    6.461604] mtk_soc_eth 1e100000.ethernet: PPE started
[    7.284281] usb usb1-port2: Cannot enable. Maybe the USB cable is bad?
[    7.647213] mtk_soc_eth 1e100000.ethernet eth0: port 3 link up
[    8.554338] usb usb1-port2: Cannot enable. Maybe the USB cable is bad?
[    8.567532] usb usb1-port2: attempt power cycle
[    9.854652] jffs2: notice: (425) jffs2_build_xattr_subsystem: complete building xattr subsystem, 7 of xdatum (3 unchecked, 4 orphan) and 122 of xref (7 dead, 0 orphan) found.
[    9.890811] mount_root: switching to jffs2 overlay
[    9.913984] overlayfs: upper fs does not support tmpfile.
[    9.944259] urandom-seed: Seeding with /etc/urandom.seed
[   10.037212] mtk_soc_eth 1e100000.ethernet: 0x100 = 0x6060000c, 0x10c = 0x80818
[   10.065013] procd: - early -
[   10.070856] procd: - watchdog -
[   10.648634] random: jshn: uninitialized urandom read (4 bytes read)
[   10.664392] usb usb1-port2: Cannot enable. Maybe the USB cable is bad?
[   10.754501] procd: - watchdog -
[   10.761570] procd: - ubus -
[   10.800911] random: ubusd: uninitialized urandom read (4 bytes read)
[   10.828818] random: ubusd: uninitialized urandom read (4 bytes read)
[   10.845925] procd: - init -
[   11.425585] kmodloader: loading kernel modules from /etc/modules.d/*
[   11.444182] ip6_tables: (C) 2000-2006 Netfilter Core Team
[   11.462858] i2c /dev entries driver
[   11.470191] ------------[ cut here ]------------
[   11.479441] WARNING: CPU: 0 PID: 559 at kernel/module.c:1138 module_put+0x48/0x5c
[   11.494354] Modules linked in: i2c_dev ledtrig_usbport nf_log_ipv6 nf_log_common ip6table_mangle ip6table_filter ip6_tables ip6t_REJECT x_tables nf_reject_ipv6 leds_gpio xhci_plat_hcd xhci_pci xhci_mtk xhci_hcd gpio_button_hotplug usbcore nls_base usb_common
[   11.539969] CPU: 0 PID: 559 Comm: kmodloader Not tainted 4.14.221 #0
[   11.552601] Stack : 00000000 00000028 86ec9288 80072a6c 805b0000 8054a1d8 00000000 00000000
[   11.569240]         80515c8c 86e69ca4 87f0dcbc 80584907 80510a20 00000001 86e69c48 5326163c
[   11.585876]         00000000 00000000 806e0000 00003290 00000000 000000af 00000007 00000000
[   11.602509]         00000000 80590000 00083d41 00000000 80000000 805b0000 00000000 8051830c
[   11.619144]         800a3d4c 00000472 00000000 00000028 00000003 8029af38 00000000 806e0000
[   11.635779]         ...
[   11.640637] Call Trace:
[   11.645513] [<8000c7b0>] show_stack+0x58/0x100
[   11.654383] [<80452f74>] dump_stack+0xa4/0xe0
[   11.663052] [<8002f798>] __warn+0xe0/0x138
[   11.671195] [<8002f880>] warn_slowpath_null+0x1c/0x2c
[   11.675258] urngd: v1.0.2 started.
[   11.681252] [<800a3d4c>] module_put+0x48/0x5c
[   11.696646] [<800a811c>] do_init_module+0x108/0x1ec
[   11.706345] [<800a72c8>] load_module+0x2080/0x2420
[   11.715874] [<800a7798>] SyS_init_module+0x130/0x18c
[   11.725761] [<80016578>] syscall_common+0x34/0x58
[   11.735281] ---[ end trace 1caef0e4861bbcf1 ]---
[   11.744512] ttyS ttyS0: 1 input overrun(s)
[   11.760541] ip_tables: (C) 2000-2006 Netfilter Core Team
[   11.779579] nf_conntrack version 0.5.0 (2048 buckets, 8192 max)
[   11.837812] xt_time: kernel timezone is -0000
[   11.854733] PPP generic driver version 2.4.2
[   11.865893] NET: Registered protocol family 24
[   11.878588] kmodloader: done loading kernel modules from /etc/modules.d/*
[   11.909106] random: crng init done
[   11.916563] random: 7 urandom warning(s) missed due to ratelimiting
[   12.194300] usb usb1-port2: Cannot enable. Maybe the USB cable is bad?
[   12.207897] usb usb1-port2: unable to enumerate USB device
[   15.918858] mtk_soc_eth 1e100000.ethernet eth0: port 4 link up
[   18.104916] mtk_soc_eth 1e100000.ethernet: PPE started
[   18.123408] br-lan: port 1(eth0.1) entered blocking state
[   18.134673] br-lan: port 1(eth0.1) entered disabled state
[   18.146191] device eth0.1 entered promiscuous mode
[   18.155850] device eth0 entered promiscuous mode
[   18.169153] br-lan: port 1(eth0.1) entered blocking state
[   18.180344] br-lan: port 1(eth0.1) entered forwarding state
[   18.192013] IPv6: ADDRCONF(NETDEV_UP): br-lan: link is not ready
[   19.105251] IPv6: ADDRCONF(NETDEV_CHANGE): br-lan: link becomes ready

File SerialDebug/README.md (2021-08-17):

这里的文件用于处理莫名其妙的串口bug

> 根据目前的debug，该错误由于从VS-keil插件迁移到CubeIDE造成

> **很可能是因为CubeIDE的gcc编译器将变量错误优化到了h750的DTCM中**

> 而h750的**DMA无法支持对DTCM进行读写**

Bug已解决

原因：CubeIDE的gcc编译器将变量错误优化到了h750的DCache中，DMA无法访问，但检测到DTCM中有被DCache映射到的数据后直接默认为完成了相关操作，于是将数据转发到串口，导致串口只输出0，并且无法通过指针按地址传递数据

解决方法：

1. 关闭DCache、ICache

2. 将独立的指针改为结构体，直接通过结构体指针传递数据

3. 使用`__attribute__`修改变量保存位置到RAM

   ```c
   __attribute__((section(".RAM_D1")))
   ```

4. 设置新的.ld文件更改变量保存位置

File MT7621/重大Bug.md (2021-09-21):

19.04版本的OpenWrt无法识别全部的系统资源

导致可用内存只有64MB

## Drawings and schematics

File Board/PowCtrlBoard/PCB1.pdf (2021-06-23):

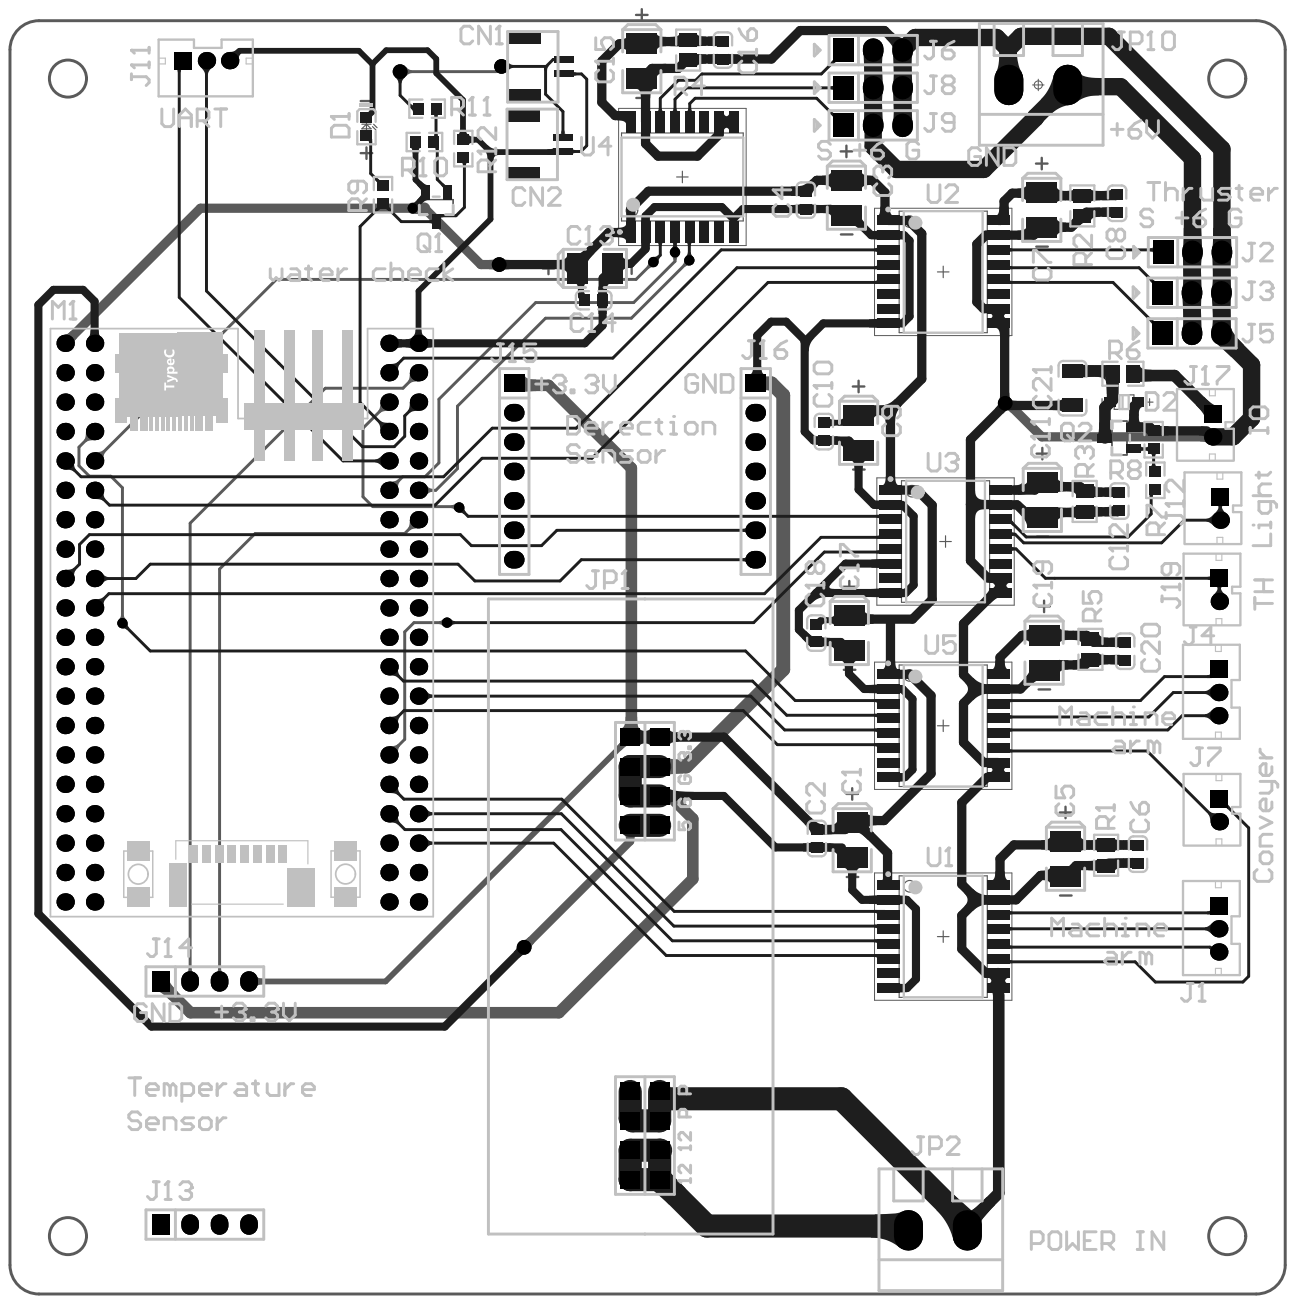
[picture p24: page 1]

Comment | Description | Designator | Footprint | LibRef | Quantity
10uF | 钽电容 | C1, C3, C5, C7, C9, C11, C13, C15, C17, C19 | CASE-B_3528 | 3528 100uF (107) 10% 6.3V | 10
0.1uF | 贴片电容 | C2, C4, C6, C8, C10, C12, C14, C16, C18, C20 | 0603_C | 0603 100nF (104) 10% 50V | 10
1uF (105) 10% 50V | 贴片电容 | C21 | 1206_C | 1206 1uF (105) 10% 50V | 1
1.25T-2AW_C722634 | | CN1, CN2 | GH-1.25 | GH 1.25T-2AW_C722634 | 2
红灯 0603 | 发光二极管 | D1 | 0603_LED_S1 | 0603 红灯 | 1
1N4148WS T4 | 二极管 | D2 | SOD-323 | SOD-323 1N4148WS T4 | 1
PH2.0-3P | | J1, J4, J11 | PH2.0-3P | PH2.0-3P | 3
HDR1x3 | Connector | J2, J3, J5, J6, J8, J9 | PIN-3-2.54-1.0 | HDR1x3 | 6
PH2.0-2P | | J7, J12, J17, J19 | PH2.0-2P | PH2.0-2P | 4
Female HDR1X4 | | J13, J14 | Fe-HDR1X4/2.54-S | Female HDR1X4 | 2
Female HDR1X7 | | J15, J16 | Fe-HDR1X7/2.54-S | Female HDR1X7 | 2
排针-座 2*4 | | JP1 | 排针-座 2*4 | 排针-座 2*4 | 1
HDR-1X2 | 2P接插件 | JP2, JP10 | KF128-5.08-2P | Header 2 | 2
FK750M2-VBT6核心板 | | M1 | FK750M2-VBT6(精简版) | FK750M2-VBT6 | 1
SS8550 Y2 | 三极管 | Q1 | SOT-23(SOT-23-3) | SOT-23 SS8550 Y2 | 1
SI2302 | MOS(场效应管) | Q2 | SOT-23(SOT-23-3) | 2N7002 7002 | 1
5.1KΩ (5101) ±1% | 贴片电阻 | R1, R2, R3, R4, R5 | 0805_R | 0805 5.1KΩ (5101) 1% | 5
330Ω (3300) ±1% | 贴片电阻 | R6 | 0805_R | 0805 330Ω (3300) 1% | 1
10KΩ (1002) ±1% | 贴片电阻 | R7 | 0603_R | 0603 10KΩ (1002) 1% | 1
4.7KΩ (4701) ±1% | 贴片电阻 | R8 | 0603_R | 0603 4.7KΩ (4701) 1% | 1
240Ω (2400) ±1% | 贴片电阻 | R9 | 0603_R | 0603 240Ω (2400) 1% | 1
27KΩ (2702) ±1% | 贴片电阻 | R10 | 0603_R | 0603 27KΩ (2702) 1% | 1
1KΩ (1001) ±1% | 贴片电阻 | R11, R12 | 0603_R | 0603 1KΩ (1001) 1% | 2
ISOW7840 | | U1, U2, U3, U4, U5 | ISOW7840 | ISOW7840 | 5

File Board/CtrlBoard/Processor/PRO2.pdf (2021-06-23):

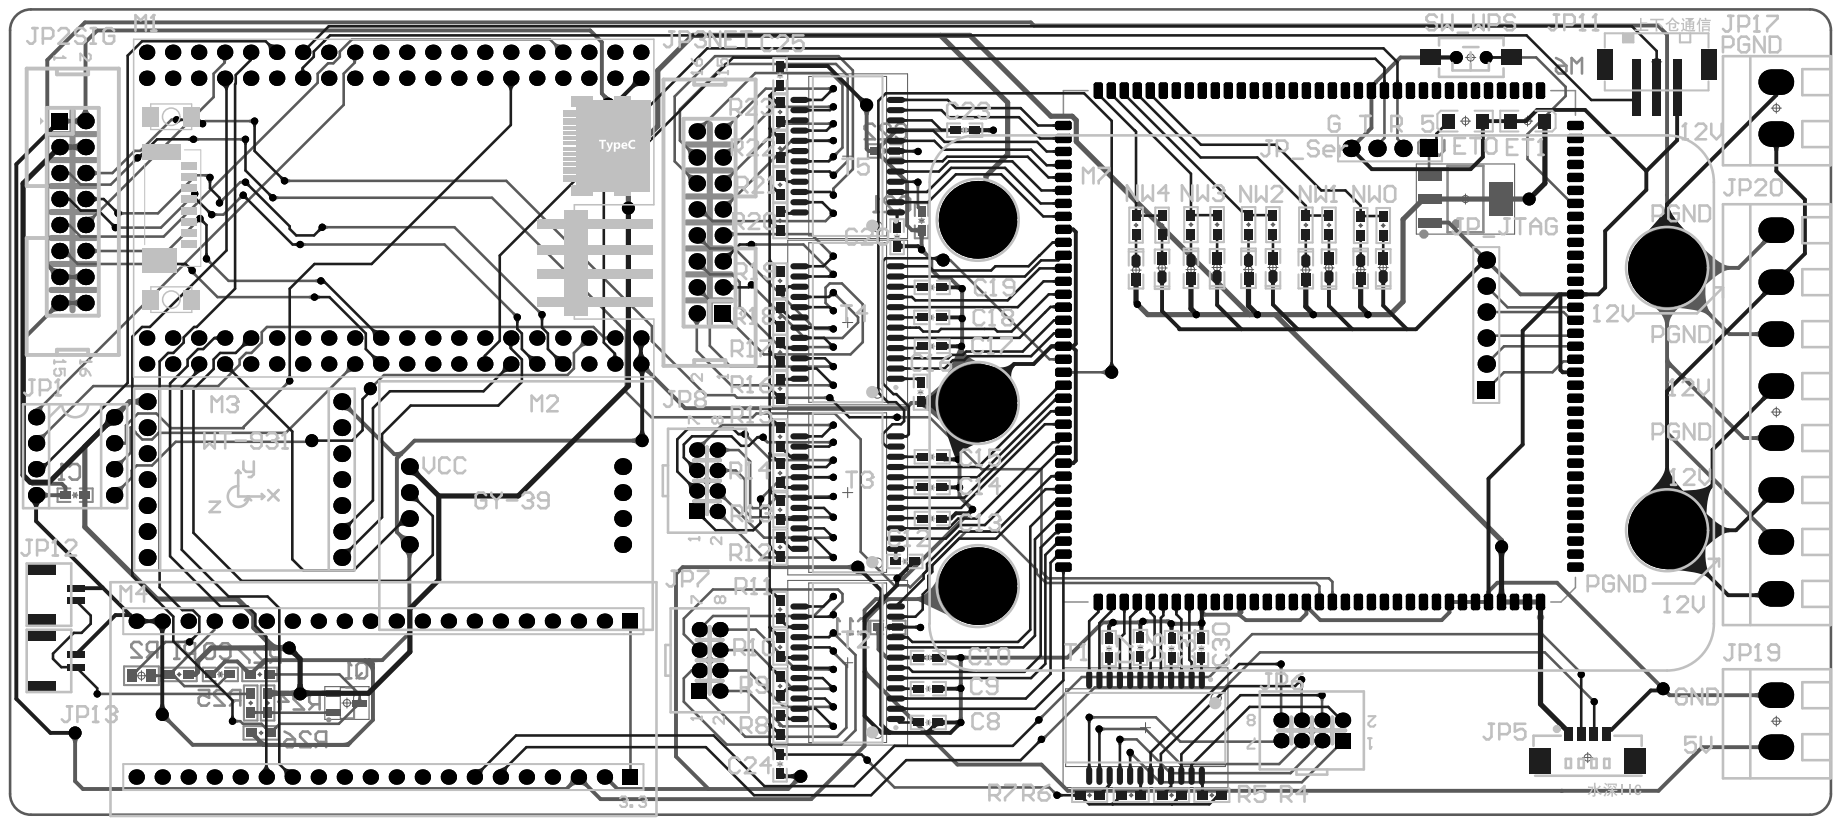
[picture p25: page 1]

Comment | Description | Designator | Footprint | LibRef | Quantity
0.01uF | 无极性贴片电容 | C0 | C 0603_M | C | 1
0.1uF | 无极性贴片电容 | C1 | C 0603_M | C | 1
0.1u | 无极性贴片电容 | C6, C7, C8, C9, C10, C11, C12, C13, C14, C15, C16, C17, C18, C19, C20, C21, C22, C23, C30, C31 | C 0603_M | C | 20
0.01u | 无极性贴片电容 | C24, C25 | C 0603_M | C | 2
10uF/6.3V | 贴片钽电容 | ET0 | CD A(3216) | C-CD | 1
22uF/6.3V | 贴片钽电容 | ET1 | CD A(3216) | C-CD | 1
DIP-8插座 | | JP1 | DIP-8座 | DIP-8插座 | 1
Header 8X2 | 8*2P接插件 | JP2, JP3 | IDC2.54-LI-2x8P | Header 8X2 | 2
HDR-1X4 | 4P接插件 | JP5 | MX 1.25-LS-4P | Header 4 | 1
水面 | 4*2P接插件 | JP6 | PHB2.0-LI-2x4P | Header 4X2 | 1
TX2 | 4*2P接插件 | JP7 | PHB2.0-LI-2x4P | Header 4X2 | 1
预留 | 4*2P接插件 | JP8 | PHB2.0-LI-2x4P | Header 4X2 | 1
HDR-1X3 | 3P接插件 | JP11 | PH2.0-LS-3P | Header 3 | 1
HDR-1X2 | 2P接插件 | JP12, JP13 | GH1.25 | Header 2 | 2
HDR-1X2 | 2P接插件 | JP17, JP19 | KF128-5.08-2P | Header 2 | 2
HDR-1X8 | 8P接插件 | JP20 | KF128-5.08-8P | Header 8 | 1
HDR-1X6 | 6P接插件 | JP_JTAG | HDR2.54-LI-6P | Header 6 | 1
HDR-1X4 | 4P接插件 | JP_Ser | HDR2.54-LI-4P | Header 4 | 1
白色 | 贴片LED | LED0_1, LED0_2 | LED 0603W | LED-SMD | 2
红色 | 贴片LED | LED1_1, LED1_2 | LED 0603R | LED-SMD | 2
蓝色 | 贴片LED | LED2_1, LED2_2 | LED 0603B | LED-SMD | 2
绿色 | 贴片LED | LED3_1, LED3_2 | LED 0603G | LED-SMD | 2
黄色 | 贴片LED | LED4_1, LED4_2 | LED 0603Y | LED-SMD | 2
FK750M2-VBT6核心板 | | M1 | FK750M2-VBT6(精简版) | FK750M2-VBT6 | 1
GY-39 | 气压温湿度光强传感 器 | M2 | GY-39 | GY-39 | 1
WT-931 | WT-931姿态角度传感器 | M3 | WT-931 | WT-931 | 1
水深解算32 | 水深传感器解算用的 stm32模块 | M4 | Deep_32 | Deep_32 | 1
HLK7621 | | M6 | HLK7621 | HLK7621 | 1
降压模块 | | M7 | 一号电压板 | 一号电压板 | 1
SS8550 | 高频放大-PNP型 | Q1 | SOT23-3M | 8550-SMD | 1
10K | 贴片电阻 | R1 | R 0603_M | R | 1
330 | 贴片电阻 | R2 | R 0805_L | R | 1
75 | 贴片电阻 | R4, R5, R6, R7, R8, R9, R10, R11, R12, R13, R14, R15, R16, R17, R18, R19, R20, R21, R22, R23 | R 0603_M | R | 20
27K | 贴片电阻 | R24 | R 0603_M | R | 1
1K | 贴片电阻 | R25, R26 | R 0603_M | R | 2
240 | 贴片电阻 | R27 | R 0603_M | R | 1
4.7K | 贴片电阻 | RL0, RL1, RL2, RL3, RL4, RL5, RL6, RL7, RL8, RL9 | R 0603_M | R | 10
3x6x5 | 3x6轻触开关 | SW_WPS | TSW SMD-3*6*2.5 | TSW 3x6 | 1
SG24002G | | T1, T2, T3, T4, T5 | SG24002G | SG24002G | 5
AMS1117-3V3 | 三端稳压芯片 | V0 | SOT223_M | AMS1117 | 1

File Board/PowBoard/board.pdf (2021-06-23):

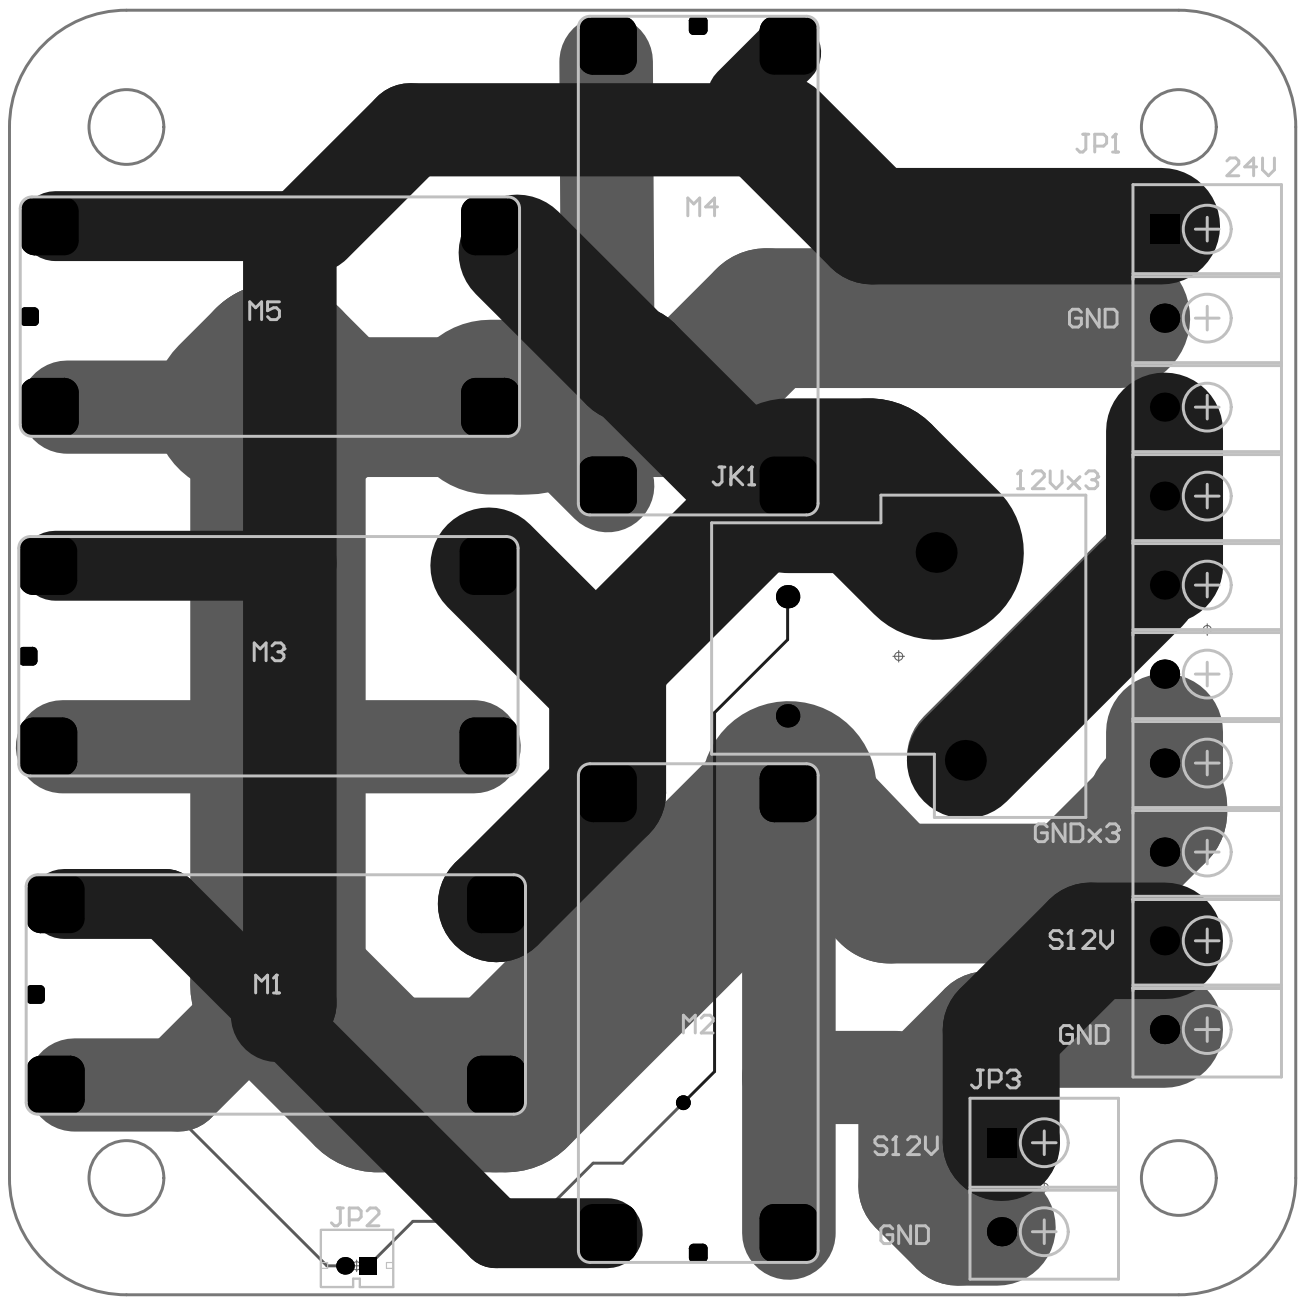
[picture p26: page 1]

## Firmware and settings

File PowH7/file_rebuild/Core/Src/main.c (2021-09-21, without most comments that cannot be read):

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
/* Includes ------------------------------------------------------------------*/
#include "main.h"
#include "cmsis_os.h"

/* USER CODE BEGIN Includes */
#include "BasicCtrl.h"
#include "Sensor.h"
/* USER CODE END Includes */


IWDG_HandleTypeDef hiwdg1;

TIM_HandleTypeDef htim1;
TIM_HandleTypeDef htim2;
TIM_HandleTypeDef htim3;
TIM_HandleTypeDef htim4;
TIM_HandleTypeDef htim5;
TIM_HandleTypeDef htim7;

UART_HandleTypeDef huart1;
UART_HandleTypeDef huart2;
UART_HandleTypeDef huart3;
DMA_HandleTypeDef hdma_usart1_rx;
DMA_HandleTypeDef hdma_usart1_tx;
DMA_HandleTypeDef hdma_usart2_rx;
DMA_HandleTypeDef hdma_usart3_rx;
DMA_HandleTypeDef hdma_usart3_tx;

osThreadId CtrlTaskHandle;
osThreadId SensorTaskHandle;
osThreadId BasetoUpTaskHandle;
osThreadId EmptyTaskHandle;
osMutexId UptoBaseDataRWFlagHandle;
osMutexId BasetoUpDataRWFlagHandle;
osMutexId WT931SensorDataRWFlagHandle;
osMutexId GY39SensorDataRWFlagHandle;
osSemaphoreId UptoBaseTransFinishHandle;
osSemaphoreId WT931TransFinishHandle;
osSemaphoreId GY39TransFinishHandle;
/* USER CODE BEGIN PV */
WT931Data WT931SensorData;
GY39Data GY39SensorData;
/* USER CODE END PV */

void SystemClock_Config(void);
void PeriphCommonClock_Config(void);
static void MX_GPIO_Init(void);
static void MX_DMA_Init(void);
static void MX_IWDG1_Init(void);
static void MX_TIM2_Init(void);
static void MX_TIM3_Init(void);
static void MX_TIM4_Init(void);
static void MX_TIM5_Init(void);
static void MX_USART1_UART_Init(void);
static void MX_USART2_UART_Init(void);
static void MX_USART3_UART_Init(void);
static void MX_TIM1_Init(void);
static void MX_TIM7_Init(void);
void CtrlTaskF(void const *argument);
void SensorTaskF(void const *argument);
void BtUF(void const *argument);
void EmptyTaskF(void const *argument);

/* USER CODE BEGIN PFP */
//void MotorAdjusterDelay(void);
///**
// * 软件PWM，可用于控制灯光PB3


// */
//void SoftwarePwm_Init(TIM_HandleTypeDef *htimx, uint16_t psr, uint16_t arr)
//{
//
//
////	htimx->Instance->PSC = psr;
////	htimx->Instance->ARR = arr;
//
//	SoftwarePwm_Control();
//
//
////	HAL_TIM_PWM_Start();
//}
/**
 *	在主程序中轮询本函数来实现PWM输出
 */
void SoftwarePwm_Control(volatile uint32_t count)
{

	if (htim7.Instance->CNT > count)
	{

		HAL_GPIO_WritePin(GPIOB, GPIO_PIN_3, GPIO_PIN_SET);
	}
	else
	{

		HAL_GPIO_WritePin(GPIOB, GPIO_PIN_3, GPIO_PIN_RESET);
	}
}
/* USER CODE END PFP */

/**
 * @brief  The application entry point.
 * @retval int
 */
int main(void)
{
	/* MCU Configuration--------------------------------------------------------*/

	/* Reset of all peripherals, Initializes the Flash interface and the Systick. */
	HAL_Init();

	/* Configure the system clock */
	SystemClock_Config();

	/* Configure the peripherals common clocks */
	PeriphCommonClock_Config();

	/* Initialize all configured peripherals */
	MX_GPIO_Init();
	MX_DMA_Init();
	MX_IWDG1_Init();
	MX_TIM2_Init();
	MX_TIM3_Init();
	MX_TIM4_Init();
	MX_TIM5_Init();
	MX_USART1_UART_Init();
	MX_USART2_UART_Init();
	MX_USART3_UART_Init();
	MX_TIM1_Init();
	MX_TIM7_Init();
	/* USER CODE BEGIN 2 */
	HAL_IWDG_Refresh(&hiwdg1);
	//继电器初始化
	HAL_GPIO_WritePin(GPIOD, GPIO_PIN_11, GPIO_PIN_RESET);

	HAL_TIM_PWM_Start(&htim1, TIM_CHANNEL_1);
	HAL_TIM_PWM_Start(&htim2, TIM_CHANNEL_1);
//	HAL_TIM_PWM_Start(&htim2, TIM_CHANNEL_2);
	__HAL_TIM_ENABLE(&htim7);
	HAL_GPIO_WritePin(GPIOB, GPIO_PIN_3, GPIO_PIN_RESET);

	HAL_TIM_PWM_Start(&htim2, TIM_CHANNEL_3);
	HAL_TIM_PWM_Start(&htim2, TIM_CHANNEL_4);
	HAL_TIM_PWM_Start(&htim3, TIM_CHANNEL_1);
	HAL_TIM_PWM_Start(&htim3, TIM_CHANNEL_2);
	HAL_TIM_PWM_Start(&htim3, TIM_CHANNEL_3);
	HAL_TIM_PWM_Start(&htim3, TIM_CHANNEL_4);
	HAL_TIM_PWM_Start(&htim4, TIM_CHANNEL_1);
	HAL_TIM_PWM_Start(&htim4, TIM_CHANNEL_2);
	HAL_TIM_PWM_Start(&htim4, TIM_CHANNEL_3);
	HAL_TIM_PWM_Start(&htim4, TIM_CHANNEL_4);
	HAL_TIM_PWM_Start(&htim5, TIM_CHANNEL_1);
	HAL_TIM_PWM_Start(&htim5, TIM_CHANNEL_2);
	HAL_TIM_PWM_Start(&htim5, TIM_CHANNEL_3);
	HAL_TIM_PWM_Start(&htim5, TIM_CHANNEL_4);

	HAL_IWDG_Refresh(&hiwdg1);
	/* USER CODE END 2 */

	/* Create the mutex(es) */
	/* definition and creation of UptoBaseDataRWFlag */
	osMutexDef(UptoBaseDataRWFlag);
	UptoBaseDataRWFlagHandle = osMutexCreate(osMutex(UptoBaseDataRWFlag));

	/* definition and creation of BasetoUpDataRWFlag */
	osMutexDef(BasetoUpDataRWFlag);
	BasetoUpDataRWFlagHandle = osMutexCreate(osMutex(BasetoUpDataRWFlag));

	/* definition and creation of WT931SensorDataRWFlag */
	osMutexDef(WT931SensorDataRWFlag);
	WT931SensorDataRWFlagHandle = osMutexCreate(osMutex(WT931SensorDataRWFlag));

	/* definition and creation of GY39SensorDataRWFlag */
	osMutexDef(GY39SensorDataRWFlag);
	GY39SensorDataRWFlagHandle = osMutexCreate(osMutex(GY39SensorDataRWFlag));

	/* USER CODE BEGIN RTOS_MUTEX */
	/* add mutexes, ... */
	/* USER CODE END RTOS_MUTEX */

	/* Create the semaphores(s) */
	/* definition and creation of UptoBaseTransFinish */
	osSemaphoreDef(UptoBaseTransFinish);
	UptoBaseTransFinishHandle = osSemaphoreCreate(
			osSemaphore(UptoBaseTransFinish), 1);

	/* definition and creation of WT931TransFinish */
	osSemaphoreDef(WT931TransFinish);
	WT931TransFinishHandle = osSemaphoreCreate(osSemaphore(WT931TransFinish),
			1);

	/* definition and creation of GY39TransFinish */
	osSemaphoreDef(GY39TransFinish);
	GY39TransFinishHandle = osSemaphoreCreate(osSemaphore(GY39TransFinish), 1);

	/* USER CODE BEGIN RTOS_SEMAPHORES */
	/* add semaphores, ... */
	/* USER CODE END RTOS_SEMAPHORES */

	/* USER CODE BEGIN RTOS_TIMERS */
	/* start timers, add new ones, ... */
	/* USER CODE END RTOS_TIMERS */

	/* USER CODE BEGIN RTOS_QUEUES */
	/* add queues, ... */
	/* USER CODE END RTOS_QUEUES */

	/* Create the thread(s) */
	/* definition and creation of CtrlTask */
	osThreadDef(CtrlTask, CtrlTaskF, osPriorityNormal, 0, 128);
	CtrlTaskHandle = osThreadCreate(osThread(CtrlTask), NULL);

	/* definition and creation of SensorTask */
	osThreadDef(SensorTask, SensorTaskF, osPriorityNormal, 0, 128);
	SensorTaskHandle = osThreadCreate(osThread(SensorTask), NULL);

	/* definition and creation of BasetoUpTask */
	osThreadDef(BasetoUpTask, BtUF, osPriorityNormal, 0, 128);
	BasetoUpTaskHandle = osThreadCreate(osThread(BasetoUpTask), NULL);

	/* definition and creation of EmptyTask */
	osThreadDef(EmptyTask, EmptyTaskF, osPriorityIdle, 0, 128);
	EmptyTaskHandle = osThreadCreate(osThread(EmptyTask), NULL);

	/* USER CODE BEGIN RTOS_THREADS */
	/* add threads, ... */
	/* USER CODE END RTOS_THREADS */

	/* Start scheduler */
	osKernelStart();

	/* We should never get here as control is now taken by the scheduler */
	/* Infinite loop */
	/* USER CODE BEGIN WHILE */
	while (1)
	{
		/* USER CODE END WHILE */

		/* USER CODE BEGIN 3 */
	}
	/* USER CODE END 3 */
}

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
/* USER CODE BEGIN Header_CtrlTaskF */
/**
 * @brief  Function implementing the CtrlTask thread.
 * @param  argument: Not used
 * @retval None
 */
/* USER CODE END Header_CtrlTaskF */
void CtrlTaskF(void const *argument)
{
	/* USER CODE BEGIN 5 */
	DownDataDef UptoBaseData =
	{ 0 };
	static MoveThruster Thurster;
	u8 Relay_filter = 0;
	u8 Relay_temp = 0;

	CaptureDownData();
	osDelay(200);
	//打开串口接收
	UptoBaseData = CaptureDownData();
	xSemaphoreGive(UptoBaseDataRWFlagHandle);
	osDelay(1);

	/* Infinite loop */
	for (;;)
	{
		if ((UptoBaseData.HeadOfData == 0x25)
				&& (UptoBaseData.EndOfData == 0x21))
		{
			if (Relay_filter >= 2) //滤波
			{
				HAL_GPIO_WritePin(GPIOD, GPIO_PIN_11, UptoBaseData.Relay);
			}

			//根据数据进行控制
			Thurster = MoveControl(UptoBaseData.StraightNum,
					UptoBaseData.RotateNum, UptoBaseData.VerticalNum,
					UptoBaseData.Mode);

			SoftwarePwm_Control(UptoBaseData.LightPWM); //软PWM灯光

			if (CheckPwmValue(Thurster.HorizontalThruster[3]))
			{
				TIM4->CCR4 = Thurster.HorizontalThruster[3]; //PD15 J6
			}
			if (CheckPwmValue(Thurster.VerticalThruster[0]))
			{
				TIM2->CCR4 = Thurster.VerticalThruster[0]; //PB11 J8
			}
			if (CheckPwmValue(Thurster.HorizontalThruster[2]))
			{
				TIM2->CCR3 = Thurster.HorizontalThruster[2]; //PB10 J9
			}
			if (CheckPwmValue(Thurster.HorizontalThruster[0]))
			{
				TIM4->CCR1 = Thurster.HorizontalThruster[0]; //PD12 J2
			}
			if (CheckPwmValue(Thurster.VerticalThruster[1]))
			{
				TIM4->CCR3 = Thurster.VerticalThruster[1]; //PD14 J3
			}
			if (CheckPwmValue(Thurster.HorizontalThruster[1]))
			{
				TIM4->CCR2 = Thurster.HorizontalThruster[1]; //PD13 J5
			}

			if (CheckPwmValue(UptoBaseData.ArmPWM[5]))
			{
				TIM2->CCR1 = UptoBaseData.ArmPWM[5]; //PA5机械臂6（预留）
			}
			if (CheckPwmValue(UptoBaseData.ArmPWM[0]))
			{
				TIM1->CCR1 = UptoBaseData.ArmPWM[0]; //PA8机械臂1
			}
			if (CheckPwmValue(UptoBaseData.ArmPWM[1]))
			{
				TIM3->CCR4 = UptoBaseData.ArmPWM[1]; //PB1机械臂2
			}
			if (CheckPwmValue(UptoBaseData.ArmPWM[2]))
			{
				TIM3->CCR3 = UptoBaseData.ArmPWM[2]; //PB0机械臂3
			}
			if (CheckPwmValue(UptoBaseData.THPWM))
			{
				TIM5->CCR1 = UptoBaseData.THPWM; //PA0云台
			}
			if (CheckPwmValue(UptoBaseData.ArmPWM[3]))
			{
				TIM3->CCR2 = UptoBaseData.ArmPWM[3]; //PA7机械臂4
			}
			if (CheckPwmValue(UptoBaseData.TranspPWM))
			{
				TIM5->CCR4 = UptoBaseData.TranspPWM; //PA3传送带
			}
			if (CheckPwmValue(UptoBaseData.ArmPWM[4]))
			{
				TIM5->CCR3 = UptoBaseData.ArmPWM[4]; //PA2机械臂5
			}
			if (CheckPwmValue(UptoBaseData.ResPWM))
			{
				TIM5->CCR2 = UptoBaseData.ResPWM; //PA1预留PWM
			}
		}

		if (xSemaphoreTake(UptoBaseTransFinishHandle,
				0) == pdTRUE)
		{
			if (xSemaphoreTake(UptoBaseDataRWFlagHandle,
					portTICK_PERIOD_MS) == pdTRUE)
			{
				//接收下传数据
				UptoBaseData = CaptureDownData();
				HAL_GPIO_TogglePin(GPIOC, GPIO_PIN_13);

				if (UptoBaseData.Relay == Relay_temp) //继电器保持原来的值
				{
					Relay_filter++; //累计变化
					if (Relay_filter >= 2)
					{
						Relay_filter = 2;
					}
				}
				else //继电器变化
				{
					Relay_filter = 0;
					Relay_temp = UptoBaseData.Relay; //暂存新值
				}

				xSemaphoreGive(UptoBaseDataRWFlagHandle);
			}
		}

		HAL_IWDG_Refresh(&hiwdg1);
	}
	/* USER CODE END 5 */
}

/* USER CODE BEGIN Header_SensorTaskF */
/**
 * @brief Function implementing the SensorTask thread.
 * @param argument: Not used
 * @retval None
 */
/* USER CODE END Header_SensorTaskF */
void SensorTaskF(void const *argument)
{
	/* USER CODE BEGIN SensorTaskF */
	//Finish:二进制信号量，串口传输结束位

	InitGY39();
	ReceiveGY39();
	ReceiveWT931();
	osDelay(200);
	GY39SensorData = ReceiveGY39();
	WT931SensorData = ReceiveWT931();
	xSemaphoreGive(GY39SensorDataRWFlagHandle);
	xSemaphoreGive(WT931SensorDataRWFlagHandle);
	/* Infinite loop */
	for (;;)
	{
		if (xSemaphoreTake(WT931TransFinishHandle,
				0) == pdTRUE)
		{
			if (xSemaphoreTake(WT931SensorDataRWFlagHandle,
					portTICK_PERIOD_MS) == pdTRUE)
			{
				WT931SensorData = ReceiveWT931();
				xSemaphoreGive(WT931SensorDataRWFlagHandle);
			}
		}
		if (xSemaphoreTake(GY39TransFinishHandle,
				0) == pdTRUE)
		{
			if (xSemaphoreTake(GY39SensorDataRWFlagHandle,
					portTICK_PERIOD_MS) == pdTRUE)
			{
				GY39SensorData = ReceiveGY39();
				xSemaphoreGive(GY39SensorDataRWFlagHandle);
			}
		}
		HAL_IWDG_Refresh(&hiwdg1);
	}
	/* USER CODE END SensorTaskF */
}

/* USER CODE BEGIN Header_BtUF */
/**
 * @brief Function implementing the BasetoUpTask thread.
 * @param argument: Not used
 * @retval None
 */
/* USER CODE END Header_BtUF */
void BtUF(void const *argument)
{
	/* USER CODE BEGIN BtUF */
	UpDataDef BasetoUpData;
	/* Infinite loop */
	for (;;)
	{
		if (xSemaphoreTake(BasetoUpDataRWFlagHandle,
				portTICK_PERIOD_MS) == pdTRUE)
		{

			BasetoUpData.CabinNum = 0b0001;
			BasetoUpData.WaterDetect = HAL_GPIO_ReadPin(GPIOD, GPIO_PIN_10)
					<< 1;

			if (xSemaphoreTake(WT931SensorDataRWFlagHandle,
					portTICK_PERIOD_MS) == pdTRUE)
			{
				BasetoUpData.AccNum[0] = WT931SensorData.AccNum[0];
				BasetoUpData.AccNum[1] = WT931SensorData.AccNum[1];
				BasetoUpData.AccNum[2] = WT931SensorData.AccNum[2];
				BasetoUpData.RotNum[0] = WT931SensorData.RotNum[0];
				BasetoUpData.RotNum[1] = WT931SensorData.RotNum[1];
				BasetoUpData.RotNum[2] = WT931SensorData.RotNum[2];
				BasetoUpData.EulNum[0] = WT931SensorData.EulNum[0];
				BasetoUpData.EulNum[1] = WT931SensorData.EulNum[1];
				BasetoUpData.EulNum[2] = WT931SensorData.EulNum[2];
				BasetoUpData.MagNum[0] = WT931SensorData.MagNum[0];
				BasetoUpData.MagNum[1] = WT931SensorData.MagNum[1];
				BasetoUpData.MagNum[2] = WT931SensorData.MagNum[2];
				xSemaphoreGive(WT931SensorDataRWFlagHandle);
			}
			if (xSemaphoreTake(GY39SensorDataRWFlagHandle,
					portTICK_PERIOD_MS) == pdTRUE)
			{
				BasetoUpData.CabinBaro = GY39SensorData.Baro;
				BasetoUpData.CabinHum = GY39SensorData.Hum;
				BasetoUpData.CabinTemperature = GY39SensorData.Temperature;
				xSemaphoreGive(GY39SensorDataRWFlagHandle);
			}

			SendUpData(BasetoUpData);
			xSemaphoreGive(BasetoUpDataRWFlagHandle);
		}
		HAL_IWDG_Refresh(&hiwdg1);
	}
	/* USER CODE END BtUF */
}

/* USER CODE BEGIN Header_EmptyTaskF */
/**
 * @brief Function implementing the EmptyTask thread.
 * @param argument: Not used
 * @retval None
 */
/* USER CODE END Header_EmptyTaskF */
void EmptyTaskF(void const *argument)
{
	/* USER CODE BEGIN EmptyTaskF */
	/* Infinite loop */
	for (;;)
	{
		HAL_IWDG_Refresh(&hiwdg1);
		osDelay(1);
	}
	/* USER CODE END EmptyTaskF */
}

/**
 * @brief  Period elapsed callback in non blocking mode
 * @note   This function is called  when TIM6 interrupt took place, inside
 * HAL_TIM_IRQHandler(). It makes a direct call to HAL_IncTick() to increment
 * a global variable "uwTick" used as application time base.
 * @param  htim : TIM handle
 * @retval None
 */
void HAL_TIM_PeriodElapsedCallback(TIM_HandleTypeDef *htim)
{
	if (htim->Instance == TIM6)
	{
		HAL_IncTick();
	}
}

/**
 * @brief  This function is executed in case of error occurrence.
 * @retval None
 */
void Error_Handler(void)
{
	/* USER CODE BEGIN Error_Handler_Debug */
	/* User can add his own implementation to report the HAL error return state */
	__disable_irq();
	while (1)
	{
	}
	/* USER CODE END Error_Handler_Debug */
}

#ifdef  USE_FULL_ASSERT
/**
  * @brief  Reports the name of the source file and the source line number
  *         where the assert_param error has occurred.
  * @param  file: pointer to the source file name
  * @param  line: assert_param error line source number
  * @retval None
  */
void assert_failed(uint8_t *file, uint32_t line)
{
  /* USER CODE BEGIN 6 */
  /* User can add his own implementation to report the file name and line number,
     ex: printf("Wrong parameters value: file %s on line %d\r\n", file, line) */
  /* USER CODE END 6 */
}
#endif /* USE_FULL_ASSERT */

/************************ (C) COPYRIGHT STMicroelectronics *****END OF FILE****/

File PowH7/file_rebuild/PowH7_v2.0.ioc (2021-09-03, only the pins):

PD8.Signal=USART3_TX
PA8.Signal=S_TIM1_CH1
PA0.Signal=S_TIM5_CH1
PB1.Signal=S_TIM3_CH4
PD12.Signal=S_TIM4_CH1
PD15.Signal=S_TIM4_CH4
PC13.Signal=GPIO_Output
PD10.Signal=GPIO_Input
PB10.Signal=S_TIM2_CH3
PB14.Signal=USART1_TX
PA5.Signal=S_TIM2_CH1
PD11.Signal=GPIO_Output
PB0.Signal=S_TIM3_CH3
Mcu.UserName=STM32H750VBTx
PB11.Signal=S_TIM2_CH4
PB15.Signal=USART1_RX
PD13.Signal=S_TIM4_CH2
PA6.Signal=S_TIM3_CH1
PD6.Signal=USART2_RX
PA3.Signal=S_TIM5_CH4
PD9.Signal=USART3_RX
PD5.Signal=USART2_TX
PA1.Signal=S_TIM5_CH2
PA2.Signal=S_TIM5_CH3
PD14.Signal=S_TIM4_CH3
PA7.Signal=S_TIM3_CH2

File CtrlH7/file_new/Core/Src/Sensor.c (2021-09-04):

/**
 * @file Sensor.c
 * @brief
 * @author Harold Zhao(zyn810039594) and RedlightASl (dddbbbdd@foxmail.com)
 * @version 1.0
 * @date 2021-08-19
 *
 * @copyright Copyright (c) 2021  RedlightASl
 *
 * @par 修改日志:
 * <table>
 * <tr><th>Date       <th>Version <th>Author  <th>Description
 * <tr><td>2021-08-19 <td>1.0     <td>wangh     <td>Content
 * </table>
 */
#include "Sensor.h"
#include <stdlib.h>

__attribute__((section(".RAM_D1")))       u8 WT931Receive[WT931_UART_RXLen] =
{ 0 };
__attribute__((section(".RAM_D1")))       u8 GY39Send[GY39_UART_TXLen] =
{ 0 };
__attribute__((section(".RAM_D1")))       u8 GY39Receive[GY39_UART_RXLen] =
{ 0 };
#ifdef CtrlSide
__attribute__((section(".RAM_D1")))       u8 DeepReceive[Deep_UART_RXLen] =
{ 0 };
__attribute__((section(".RAM_D1")))       u8 P30Send[P30_UART_TXLen] =
{ 0 };
__attribute__((section(".RAM_D1")))       u8 P30Receive[P30_UART_RXLen] =
{ 0 };
#endif

/**
 * @brief GY39温湿度大气压传感器初始化
 */
void InitGY39(void)
{
	GY39Send[0] = 0xa5;
	GY39Send[1] = 0x82;
	GY39Send[2] = 0x27;

	HAL_UART_Transmit_DMA(&GY39_UART, GY39Send, GY39_UART_TXLen);
}

/**
 * @brief 接收GY39温湿度大气压传感器数据
 * @return GY39Data GY39传感器数据接收结构体
 */
GY39Data ReceiveGY39(void)
{
	GY39Data RevGY39;

	RevGY39.Temperature = ((GY39Receive[4] << 8) | GY39Receive[5]);
	RevGY39.Baro = ((GY39Receive[8] << 24) | (GY39Receive[9] << 16)
			| (GY39Receive[7] << 8) | GY39Receive[6]);
	RevGY39.Hum = ((GY39Receive[10] << 8) | GY39Receive[11]);

	__HAL_UART_ENABLE_IT(&GY39_UART, UART_IT_IDLE);
	HAL_UART_Receive_DMA(&GY39_UART, GY39Receive, GY39_UART_RXLen);

	return RevGY39;
}

/**
 * @brief 接收WT931九轴传感器数据
 * @return WT931Data WT931九轴传感器数据结构体
 */
WT931Data ReceiveWT931(void)
{
	WT931Data RevWT931;

	for (int i = 0; i < WT931_UART_RXLen; i++)
	{
		if ((WT931Receive[i] == 0x55) && (WT931Receive[i + 1] == 0x51))
		{
			RevWT931.AccNum[0] = ((WT931Receive[i + 3] << 8)
					| WT931Receive[i + 2]);
			RevWT931.AccNum[1] = ((WT931Receive[i + 5] << 8)
					| WT931Receive[i + 4]);
			RevWT931.AccNum[2] = ((WT931Receive[i + 7] << 8)
					| WT931Receive[i + 6]);
		}
		else if ((WT931Receive[i] == 0x55) && (WT931Receive[i + 1] == 0x52))
		{
			RevWT931.RotNum[0] = ((WT931Receive[i + 3] << 8)
					| WT931Receive[i + 2]);
			RevWT931.RotNum[1] = ((WT931Receive[i + 5] << 8)
					| WT931Receive[i + 4]);
			RevWT931.RotNum[2] = ((WT931Receive[i + 7] << 8)
					| WT931Receive[i + 6]);
		}
		else if ((WT931Receive[i] == 0x55) && (WT931Receive[i + 1] == 0x53))
		{
			RevWT931.EulNum[0] = ((WT931Receive[i + 3] << 8)
					| WT931Receive[i + 2]);
			RevWT931.EulNum[1] = ((WT931Receive[i + 5] << 8)
					| WT931Receive[i + 4]);
			RevWT931.EulNum[2] = ((WT931Receive[i + 7] << 8)
					| WT931Receive[i + 6]);
		}
		else if ((WT931Receive[i] == 0x55) && (WT931Receive[i + 1] == 0x54))
		{
			RevWT931.MagNum[0] = ((WT931Receive[i + 3] << 8)
					| WT931Receive[i + 2]);
			RevWT931.MagNum[1] = ((WT931Receive[i + 5] << 8)
					| WT931Receive[i + 4]);
			RevWT931.MagNum[2] = ((WT931Receive[i + 7] << 8)
					| WT931Receive[i + 6]);
		}
	}

//	if ((WT931Receive[0] == 0x55) && (WT931Receive[1] == 0x51))
//	{
//		RevWT931.AccNum[0] = ((WT931Receive[3] << 8) | WT931Receive[2]);
//		RevWT931.AccNum[1] = ((WT931Receive[5] << 8) | WT931Receive[4]);
//		RevWT931.AccNum[2] = ((WT931Receive[7] << 8) | WT931Receive[6]);
//	}
//
//	if ((WT931Receive[11] == 0x55) && (WT931Receive[12] == 0x52))
//	{
//		RevWT931.RotNum[0] = ((WT931Receive[14] << 8) | WT931Receive[13]);
//		RevWT931.RotNum[1] = ((WT931Receive[16] << 8) | WT931Receive[15]);
//		RevWT931.RotNum[2] = ((WT931Receive[18] << 8) | WT931Receive[17]);
//	}
//
//	if ((WT931Receive[22] == 0x55) && (WT931Receive[23] == 0x53))
//	{
//		RevWT931.EulNum[0] = ((WT931Receive[25] << 8) | WT931Receive[24]);
//		RevWT931.EulNum[1] = ((WT931Receive[27] << 8) | WT931Receive[26]);
//		RevWT931.EulNum[2] = ((WT931Receive[29] << 8) | WT931Receive[28]);
//	}
//
//	if ((WT931Receive[33] == 0x55) && (WT931Receive[34] == 0x54))
//	{
//		RevWT931.MagNum[0] = ((WT931Receive[36] << 8) | WT931Receive[35]);
//		RevWT931.MagNum[1] = ((WT931Receive[38] << 8) | WT931Receive[37]);
//		RevWT931.MagNum[2] = ((WT931Receive[40] << 8) | WT931Receive[39]);
//	}

//	RevWT931.AccNum[0] = ((WT931Receive[3] << 8) | WT931Receive[2]);
//	RevWT931.AccNum[1] = ((WT931Receive[5] << 8) | WT931Receive[4]);
//	RevWT931.AccNum[2] = ((WT931Receive[7] << 8) | WT931Receive[6]);
//
//	RevWT931.RotNum[0] = ((WT931Receive[14] << 8) | WT931Receive[13]);
//	RevWT931.RotNum[1] = ((WT931Receive[16] << 8) | WT931Receive[15]);
//	RevWT931.RotNum[2] = ((WT931Receive[18] << 8) | WT931Receive[17]);
//
//	RevWT931.EulNum[0] = ((WT931Receive[25] << 8) | WT931Receive[24]);
//	RevWT931.EulNum[1] = ((WT931Receive[27] << 8) | WT931Receive[26]);
//	RevWT931.EulNum[2] = ((WT931Receive[29] << 8) | WT931Receive[28]);
//
//	RevWT931.MagNum[0] = ((WT931Receive[36] << 8) | WT931Receive[35]);
//	RevWT931.MagNum[1] = ((WT931Receive[38] << 8) | WT931Receive[37]);
//	RevWT931.MagNum[2] = ((WT931Receive[40] << 8) | WT931Receive[39]);
	__HAL_UART_ENABLE_IT(&WT931_UART, UART_IT_IDLE);
	HAL_UART_Receive_DMA(&WT931_UART, WT931Receive, WT931_UART_RXLen);

//	HAL_UART_Receive_DMA(&WT931_UART, WT931Receive, 45);

	return RevWT931;
}

#ifdef CtrlSide
/**
 * @brief 接收水深水温传感器数据
 * @return DeepData 水深水温传感器数据结构体
 */
DeepData ReceiveDeep(void)
{
	DeepData RevDeep;

//	RevDeep.WaterDepth = ((DeepReceive[1] << 8) | DeepReceive[0]);
//	RevDeep.WaterTemperature = ((DeepReceive[3] << 8) | DeepReceive[2]);

	u8 temperature_origin_data[4] =
	{ 0 };
	u8 depth_origin_data[3] =
	{ 0 };

	for (int i = 0; i < Deep_UART_RXLen; i++)
	{
		if ((DeepReceive[i] == 'T') && (DeepReceive[i + 1] == '='))
		{ //解析温度
			if ((DeepReceive[i + 2] >= '0') && (DeepReceive[i + 2] <= '9'))
			{ //温度为正
				temperature_origin_data[0] = DeepReceive[i + 2] - '0';
				temperature_origin_data[1] = DeepReceive[i + 3] - '0';
				temperature_origin_data[2] = DeepReceive[i + 5] - '0';
				temperature_origin_data[3] = DeepReceive[i + 6] - '0';
			}
			else if (DeepReceive[i + 2] == '-')
			{ //温度为负
				temperature_origin_data[0] = DeepReceive[i + 3] - '0';
				temperature_origin_data[1] = DeepReceive[i + 4] - '0';
				temperature_origin_data[2] = DeepReceive[i + 6] - '0';
				temperature_origin_data[3] = DeepReceive[i + 7] - '0';
			}
		}
		else if ((DeepReceive[i] == 'D') && (DeepReceive[i + 1] == '='))
		{ //解析深度
			if (DeepReceive[i + 2] == '-')
			{ //深度为负
				depth_origin_data[0] = DeepReceive[i + 3] - '0';
				depth_origin_data[1] = DeepReceive[i + 5] - '0';
				depth_origin_data[2] = DeepReceive[i + 6] - '0';
			}
			else if ((DeepReceive[i + 2] >= '0') && (DeepReceive[i + 2] <= '9'))
			{ //深度为正
				depth_origin_data[0] = DeepReceive[i + 2] - '0';
				depth_origin_data[1] = DeepReceive[i + 4] - '0';
				depth_origin_data[2] = DeepReceive[i + 5] - '0';
			}
		}
	}
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

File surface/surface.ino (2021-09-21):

/**
   @file surface.ino
   @brief
   @author RedlightASl (dddbbbdd@foxmail.com)
   @version 1.0
   @date 2021-08-21

   @copyright Copyright (c) 2021  RedlightASl

   @par 修改日志:
   <table>
   <tr><th>Date       <th>Version <th>Author  <th>Description
   <tr><td>2021-08-21 <td>1.0     <td>wangh     <td>Content
   </table>
*/
#include "surface.h"

#ifndef DO_NOT_USING_IT_FLAG
#include <FlexiTimer2.h>
#endif

/* 字符串输出变量 */
u8 WATER_WARNING = 0; //漏水警报
signed char WATER_WARNING_TIMER_COUNT = 0; //漏水警报计时

int StrightNum = 1500; //前进后退 A0
int RotateNum = 1500; //旋转侧推 A0
int VerticalNum = 1500; //垂直 A5
long LightNum = 0; //灯光 A2
int CameraPanNum = 1500; //云台 A4
int ConveyerNum = 1500; //传送带 A3
int MachineArm_HorizentalNum = 1500; //水平机械臂 A11
int MachineArm_LargeNum = 1500; //大臂 A12
int MachineArm_MiddleNum = 1500; //中臂 A13
int MachineArm_SmallNum = 1500; //小臂 A14
int MachineArm_CatchingNum = 1500; //夹取 A15
int ReservedNum = 1500; //保留位PWM控制数据
int UserANum = 1500; //自定义旋钮A A6
int UserBNum = 1500; //自定义旋钮B A7

/* 按钮控制变量 */
u8 KeepDeepNum = 0;
u8 KeepDepth_FLAG = 0; //定深模式控制
u8 KeepOrbitNum = 0;
u8 KeepOrbit_FLAG = 0; //定向模式控制
u8 ControlButtonNum = 0;
u8 Control_FLAG = 0; //控制权限
u8 ArmNum = 0;
u8 MachineArm_ALL_Switch_FLAG = 0; //机械臂总开关
u8 KeepDownNum = 0;
u8 MachineArm_A_Switch_FLAG = 0; //机械臂A开关 下潜保持
u8 TransSwitchNum = 0;
u8 MachineArm_B_Switch_FLAG = 0; //机械臂B开关 传送带 启用
u8 SideNum = 0;
u8 Mode_FLAG = 0; //侧推旋转模式控制

/* 一键抓取标志位与变量 */
u8 GrabStart_FLAG = 0; //开始一键抓取
u8 GrabState = 0; //一键抓取状态机标志

int AutoGrab_ClipNum = 1500; //一键抓取夹手
int AutoGrab_FlipNum = 1500; //一键抓取旋转臂

u16 FInitTime=0; //准备时间变量
u16 FClipTime = 0; //维持夹手张开时间变量
u16 FFlipTime = 0; //维持翻转时间变量

u8 LateBuf = 0; //回传延时标志位

static void PrintBlank()
{
	for (int r = 0;r < 60;r++)
	{
		for (int k = 0;k < 1000;k++)
		{
			for (int j = 0;j < 1000;j++)
			{
				for (int i = 0; i < 32; i++)
				{
					NOP;
				}
			}
		}
	}
}

#ifndef DO_NOT_USING_IT_FLAG
/**
   @brief 定时器中断服务程序
*/
void TimerInterrupt()
{
	// if (LateBuf > 4)
	// {
	// 	Serial.flush();
	// 	delay(1);
	// 	Surface_IT_SendSerialMesg();
	// 	Serial.flush();
	// 	LateBuf = 0;
	// }

	//一键抓取状态机
	// if ((GrabStart_FLAG) && (LateBuf % 4 == 0))
	if(GrabStart_FLAG)
	{
		switch (GrabState)
		{
		case 0: //初始状态
			AutoGrab_ClipNum = INIT_CLIP_ANGLE; //初始化抓取舵机
			AutoGrab_FlipNum = INIT_FLIP_ANGLE; //初始化翻转舵机
			FInitTime++;
			if(FInitTime == 2)
			{
				FInitTime=0;
				GrabState = 1; //状态转移
			}
			break;
		case 1: //夹手合紧，不翻转
			AutoGrab_ClipNum = CLIP_ANGLE;
			AutoGrab_FlipNum = INIT_FLIP_ANGLE;
			FClipTime++;
			if (FClipTime == DoClipTime)
			{
				FClipTime = 0;
				GrabState = 2; //状态转移
			}
			break;
		case 2: //夹手合紧，翻转
			AutoGrab_ClipNum = CLIP_ANGLE;
			AutoGrab_FlipNum = FLIP_ANGLE;
			FFlipTime++;
			if (FFlipTime == DoFlipTime)
			{
				FFlipTime = 0;
				GrabState = 3; //状态转移
			}
			break;
		case 3: //夹手松开，之后恢复原状
			AutoGrab_ClipNum = INIT_CLIP_ANGLE;
			AutoGrab_FlipNum = FLIP_ANGLE;
			FClipTime++;
			if (FClipTime == DoDisClipTime)
			{
				FClipTime = 0;
				GrabState = 0; //回到原始状态
				GrabStart_FLAG = 0;
			}
			break;
		}
	}
	LateBuf++;
}
#endif

void setup()
{
	Serial.begin(UPLOAD_SERIAL_BAUDRATE);

	pinMode(WATER_DETECTED_WARNING, OUTPUT); //指示漏水警报

	/* 初始化开关控制引脚 */
	pinMode(KEEP_DEPTH_BUTTON, INPUT); //定深开关
	pinMode(ROOT_BUTTON, INPUT); //控制权限开关
	pinMode(MACHINE_ARM_A_BUTTON, INPUT); //机械臂A开关 下潜保持
	pinMode(MACHINE_ARM_ALL_BUTTON, INPUT); //机械臂总开关
	pinMode(MACHINE_ARM_B_BUTTON, INPUT); //机械臂B开关 传送带自动启用
	pinMode(SIDE_PUSH_MODE_SWITCH_BUTTON, INPUT); //侧推模式开关
	pinMode(KEEP_ORBIT_BUTTON, INPUT); //定向开关

#ifndef DO_NOT_USING_IT_FLAG
	FlexiTimer2::set(Latency, TimerInterrupt);
	FlexiTimer2::start();
#endif
}

void loop()
{
	Surface_Task_Control();
	Surface_Task_ReadSerialData();
	Surface_Task_SendSerialMesg();
}

/**
   @brief 实时读取控制按钮和控制杆数据
*/
void Surface_Task_Control()
{
	/* 读取基本控制数据 */
	StrightNum = map(analogRead(FORWARD_PIN), 0, 1023, 2300, 700);
	RotateNum = map(analogRead(ROTATE_PIN), 0, 1023, 700, 2300);
	VerticalNum = map(analogRead(VERTICAL_PIN), 0, 1023, 2300, 700);
	LightNum = map(analogRead(LIGHT_PIN), 0, 1023, 0, 65535);
	CameraPanNum = map(analogRead(CAMERA_PAN_PIN), 0, 1023, 2250, 1000);
	ConveyerNum = map(analogRead(Conveyer_PIN), 0, 1023, 2500, 500);

	/* 读取机械臂控制数据 */
	// MachineArm_HorizentalNum = map(analogRead(MACHINE_ARM_HORIZENTAL_PIN), 0, 800, 2500, 500); //小臂
	// MachineArm_LargeNum = map(analogRead(MACHINE_ARM_LARGE_PIN), 300, 1023, 2500, 500); //大臂
	// MachineArm_MiddleNum = map(analogRead(MACHINE_ARM_MIDDLE_PIN), 0, 1023, 2500, 800); //中臂
	// MachineArm_SmallNum = map(analogRead(MACHINE_ARM_SMALL_PIN), 0, 1023, 500, 2500); //水平
	// MachineArm_CatchingNum = map(analogRead(MACHINE_ARM_CATCHING_PIN), 0, 1023, 1700, 1000); //夹手

	/* 读取其他旋钮数据 */
	UserANum = map(analogRead(USER_PIN_A), 0, 1023, 500, 2500); //自定义旋钮A 旋转臂
	UserBNum = map(analogRead(USER_PIN_B), 0, 1023, 500, 2500); //自定义旋钮B 新夹手

	/* 读取按钮数据 */
	if (ControlButtonNum != digitalRead(ROOT_BUTTON)) //主控权限开关
	{
		ControlButtonNum = digitalRead(ROOT_BUTTON);
		// Control_FLAG = 1;
	}
	if (KeepDeepNum != digitalRead(KEEP_DEPTH_BUTTON)) //定深开关
	{
		KeepDeepNum = digitalRead(KEEP_DEPTH_BUTTON);
		// KeepDepth_FLAG = 1;
	}
	if (KeepOrbitNum != digitalRead(KEEP_ORBIT_BUTTON)) //定向开关 一键抓取
	{
		KeepOrbitNum = digitalRead(KEEP_ORBIT_BUTTON);
		// KeepOrbit_FLAG = 1;
	}
	if (ArmNum != digitalRead(MACHINE_ARM_ALL_BUTTON)) //机械臂控制开关 直接控制继电器
	{
		ArmNum = digitalRead(MACHINE_ARM_ALL_BUTTON);
		// MachineArm_ALL_Switch_FLAG = 1;
	}
	if (SideNum != digitalRead(SIDE_PUSH_MODE_SWITCH_BUTTON)) //侧推模式开关
	{
		SideNum = digitalRead(SIDE_PUSH_MODE_SWITCH_BUTTON);
		// Mode_FLAG = 1;
	}
	if (KeepDownNum != digitalRead(MACHINE_ARM_A_BUTTON)) //下潜保持开关
	{
		KeepDownNum = digitalRead(MACHINE_ARM_A_BUTTON);
		// MachineArm_A_Switch_FLAG = 1;
	}
	if (TransSwitchNum != digitalRead(MACHINE_ARM_B_BUTTON)) //传送带启用开关
	{
		TransSwitchNum = digitalRead(MACHINE_ARM_B_BUTTON);
		// MachineArm_B_Switch_FLAG = 1;
	}

	//一键抓取
	if (digitalRead(KEEP_ORBIT_BUTTON))
	{
		GrabStart_FLAG = 1;
	}
}

/**
   @brief 读取漏水数据并通知定时器中断服务函数进行处理
*/
void Surface_Task_ReadSerialData()
{
	static u8 isRev;
	if (Serial.available())
	{
		isRev = Serial.read();
		if (isRev == '1')
		{
			WATER_WARNING = 1;
		}
		else if (isRev == '0')
		{
			WATER_WARNING = 0;
		}
	}
	WaterHandler();
}
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

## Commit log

2021-04-20 PCB Designing
    [Ctrlboard.PrjPCB, board.SchDoc]
2021-04-25 Some board document
    [Ctrlboard.PrjPCB, PRO.PcbDoc, PRO1.SchDoc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]
2021-04-28 PCB update
    [Connect.PcbDoc, Connect.SchDoc, Connect.step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]
2021-04-29 pcb reflesh
    [PCB1.PcbDoc]
2021-05-18 Final hardware update and first software beginning
    We have finished the hardware design of the machine, and tested successfully. And now, we focus on the software building.
    [Connect.xlsx, CtrlH7 Debug.cfg, Ctrlboard.PrjPCB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]
2021-06-15 Functional Update
    Several changes,but I can't explain.
    [DownFormat.xlsx, PCB1.PcbDoc, PRO1.SchDoc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]
2021-06-15 New Version of Horizonal Powerboard
    A new PCB design.
    [Hpowerv2.SchDoc, horziontal_powerboard_v2.PrjPcb, s_pboard.PrjPCB]
2021-06-22 Add Depth Sensor Analyse Process
    [Hpowerv2.SchDoc]
2021-06-23 Daily Update
    I don't know what I have changed T-T
    [PCB_Project1.PrjPCB]
2021-06-27 Update README docs
    [Hpowerv2.SchDoc, PCB_Project1.PrjPCB, horziontal_powerboard_v2.PrjPcb]
2021-06-27 Update ADPrj
    [Hpowerv2.SchDoc, Powerboard_2.PrjPcb, Proconnect.PrjPCB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]
2021-07-03 Update SCH
    [Hpowerv2.SchDoc, PRO1.SchDoc, PRO2.SchDoc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]
2021-07-04 Update Debug
    [PowH7.cfg]
2021-07-06 Update MT7621
    [HLK-7621-ALL-KIT-V2.2.PcbDoc, HLK-7621-ALL-KIT-V2.2.SchDoc]
2021-07-07 Update Program
    [DownFormat.xlsx, connector.SchDoc]
2021-08-01 Rebulid PowerH7
    We use signal and structure for the first time.
2021-08-06 Update ROVlibs and layout Debugs
    [DownFormat.xlsx, UpFormat.xlsx]
2021-08-22 Update format
    [UpFormat.xlsx]
2021-08-30 Update Main
    [Ctrlboard.PrjPCB, board.SchDoc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]
2021-09-02 Update Control Debug
    [DownFormat.xlsx, UpFormat.xlsx]
2021-09-04 Finish Sensor
2021-09-25 Finish Project
    [Data200320042405.tsv, JY901.OBJ, STARTUP.OBJ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]

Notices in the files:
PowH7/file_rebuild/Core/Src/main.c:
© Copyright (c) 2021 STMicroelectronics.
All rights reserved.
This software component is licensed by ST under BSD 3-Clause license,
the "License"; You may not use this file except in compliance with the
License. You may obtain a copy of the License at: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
